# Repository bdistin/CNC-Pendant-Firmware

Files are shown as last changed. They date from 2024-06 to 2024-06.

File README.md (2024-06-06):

# CNC-Pendant-Firmware

This is firmware to run on an Arduino Pro Micro (preferred) or Arduino Nano to interface a popular style of wired CNC pendant to the PanelDue port of Duet electronics. Build it using Arduino IDE. 

For a full guide to building the pendant, see [the Duet3D wiki here](https://docs.duet3d.com/en/User_manual/Connecting_hardware/IO_CNC_Pendant).

## Fork Notes

This is a fork meant to adapt a D15 ended MPG. This has minor modifications due to the specific wiring of an off the shelf MPG. Please verify your specific MPG wiring
against the below diagram. 
```
     ________________________________________
    / GND  A-   B-   YIN  4    X10   EP      \
   / 5v   A+   B+   XIN  ZIN  X100  5    COM  \
   --------------------------------------------
     ______________________
    / 9  10 11 12 13 14 15 \
   / 1  2  3  4  5  6  7  8 \
   --------------------------
```
Because of the available pins this is slightly less capable than the Head of this fork. There is no way to control the LED, nor a way to differenciate between No Axis
and the 6th Axis. The X1 multiplier setting is possible with the adjusted logic in this fork by only checking the X10/X100 pins.

## Pendant to Arduino Pro Micro connections

| Function | D15 Pin | Pro Micro |
|:---|:---|:---|
| 5v | 1 | VCC |
| A+ | 2 | D10 |
| B+ | 3 | D14 |
| XIN | 4 | D2 |
| ZIN | 5 | D4 |
| X100 | 6 | D6 |
| Axis5 | 7 | D9 |
| GND/COM | 8, 9, 16 | GND |
| YIN | 12 | D3 |
| Axis4 | 13 | D5 |
| X10 | 14 | D7 |
| EStop | 15 | D8 |

Arduino Pro Micro to Duet 3 IO_0 connector or Duet 2 PanelDue connector wiring (3- or 4-core cable):

| Pro Micro | Duet |
|:---|:-----|
| VCC | +5V (red wire) |
| GND | GND (yellow wire) |
| TXO<br>GND | Through 6K8 resistor to IO_0_IN (Duet 3) or URXD0 (Duet 2)<br>Also connect 10K resistor between GND and IO_0_IN (Duet 3) or URXD0 (Duet 2) (blue wire from resistor junction to Duet) |

To connect a PanelDue as well (the Arduino Pro Micro passes the PanelDue commands through to the Duet):

| PanelDue | Pro Micro / Duet |
|:---|:---|
| +5V | +5V/VCC (red wire to Ardiuno or Duet) |
| GND | GND (yellow wire to Ardiuno or Duet) |
| DIN | **Duet** IO_0_OUT (Duet 3) or UTXD0 (Duet 2) (green wire) |
| DOUT | **Pro Micro** RXI (blue wire of PanelDue cable to green wire of pendant cable) |

For wiring differences and hardware changes needed if using an Arduino Nano, see the comments at the start of the CNC-pendant.ino file.

## Support requests

Please use the [forum](https://forum.duet3d.com) for support requests.

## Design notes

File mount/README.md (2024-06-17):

# Din Rail Mount
This is a printable model to adapt the PCB to a din rail mount using the Voron Din Clip found here: https://github.com/VoronDesign/Voron-Trident/blob/main/STLs/ElectronicsBay/pcb_din_clip_x3.stl

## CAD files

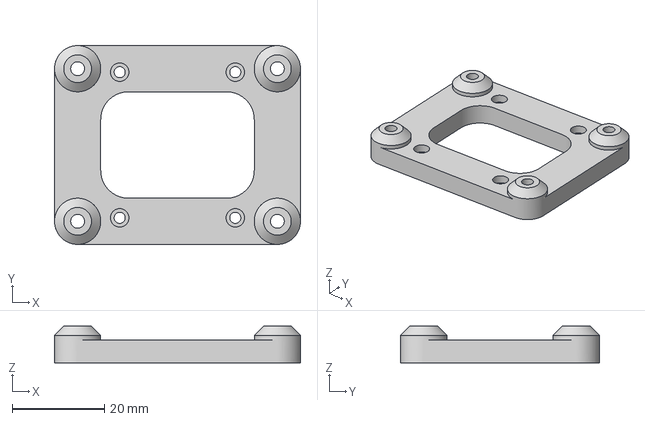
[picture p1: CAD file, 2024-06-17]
mount/Din Mount Adapter.3mf
53.2 x 43.0 x 8.00 mm

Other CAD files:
mount/Din Mount Adapter.f3d

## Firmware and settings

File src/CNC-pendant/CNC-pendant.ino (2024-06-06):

// CNC pendant interface to Duet
// D Crocker, started 2020-05-04

/* This Arduino sketch can be run on either Arduino Nano or Arduino Pro Micro. 
 * It should alo work on an Arduino Uno (using the same wiring scheme as for the Nano) or Arduino Leonardo (using the same wiring scheme as for the Pro Micro).
 * The recommended board is the Arduino Pro Micro because the passthrough works without any modificatoins to the Arduino. 

/* This is a fork meant to adapt a D15 ended MPG. This has minor modifications due to the specific wiring of an off the shelf MPG. Please verify your specific MPG wiring
 * against the below diagram. 
 *   ________________________________________
 *  / GND  A-   B-   YIN  4    X10   ES      \
 * / 5v   A+   B+   XIN  ZIN  X100  5    COM  \
 * --------------------------------------------
 *   ______________________
 *  / 9  10 11 12 13 14 15 \
 * / 1  2  3  4  5  6  7  8 \
 * --------------------------
 * Note: Because of the available pins this is slightly less capable than the Head of this fork. There is no way to control the LED, nor a way to differentiate between No Axis
 * and the 6th Axis. The X1 multiplier setting is possible with the adjusted logic in this fork by only checking the X10/X100 pins.

*** Pendant to Arduino Pro Micro connections ***

Function    D15 Pin    Pro Micro
5v          1          VCC
A+          2          D10
B+          3          D14
XIN         4          D2
ZIN         5          D4
X100        6          D6
Axis5       7          D9
GND/COM     8, 9, 16   GND
YIN         12         D3
Axis4       13         D5
X10         14         D7
EStop       15         D8

*** Arduino Pro Micro to Duet PanelDue connector connections ***

Pro Micro Duet
VCC       +5V
GND       GND
TX1/D0    Through 6K8 resistor to URXD, also connect 10K resistor between URXD and GND

To connect a PanelDue as well:

PanelDue +5V to +5V/VCC
PanelDue GND to GND
PanelDue DIN to Duet UTXD or IO_0_OUT
PanelDue DOUT to /Pro Micro RX1/D0.

*** Arduino Nano to Duet PanelDue connector connections ***

Nano    Duet
+5V     +5V
GND     GND
TX1/D0  Through 6K8 resistor to URXD, also connect 10K resistor between URXD and GND

To connect a PanelDue as well:

PanelDue +5V to +5V
PanelDue GND to GND
PanelDue DIN to Duet UTXD or IO_0_OUT
PanelDue DOUT to Nano/Pro Micro RX1/D0.

On the Arduino Nano is necessary to replace the 1K resistor between the USB interface chip by a 10K resistor so that PanelDiue can override the USB chip.
On Arduino Nano clones with CH340G chip, it is also necessary to remove the RxD LED or its series resistor.

*/

// Configuration constants
const int PinA = 10;
const int PinB = 14;
const int PinX = 2;
const int PinY = 3;
const int PinZ = 4;
const int PinAxis4 = 5;
const int PinAxis5 = 9;
const int PinStop = 8;
const int PinTimes10 = 7;
const int PinTimes100 = 6;

const unsigned long BaudRate = 57600;
const int PulsesPerClick = 4;
const unsigned long MinCommandInterval = 20;
const int HoldTime = 1000;

// Table of commands we send, one entry for each axis
const char* const MoveCommands[] = {
  "G91 G0 F6000 X",     // X axis
  "G91 G0 F6000 Y",     // Y axis
  "G91 G0 F600 Z"      // Z axis
};

const char* Home = "G28";
const char* Park = "G27";
const char* EStop = "M112";
const char* Recover = "M999";

#include "RotaryEncoder.h"
#include "GCodeSerial.h"
#include "PassThrough.h"

RotaryEncoder encoder(PinA, PinB, PulsesPerClick);
PassThrough passThrough;

int serialBufferSize;
uint32_t whenLastCommandSent = 0;

const int axisPins[] = { PinX, PinY, PinZ, PinAxis4, PinAxis5 };

// Auto count axis array
const int numAxis = sizeof(axisPins) / sizeof(int);

#if defined(__AVR_ATmega32U4__)     // Arduino Leonardo or Pro Micro
# define UartSerial   Serial1
#elif defined(__AVR_ATmega328P__)   // Arduino Uno or Nano
# define UartSerial   Serial
#endif

GCodeSerial output(UartSerial);

// Prototype
void sendCommand(char* command, int distance=0);

// Setup
void setup() {
  pinMode(PinA, INPUT_PULLUP);
  pinMode(PinB, INPUT_PULLUP);
  pinMode(PinX, INPUT_PULLUP);
  pinMode(PinY, INPUT_PULLUP);
  pinMode(PinZ, INPUT_PULLUP);
  pinMode(PinAxis4, INPUT_PULLUP);
  pinMode(PinAxis5, INPUT_PULLUP);
  pinMode(PinTimes10, INPUT_PULLUP);
  pinMode(PinTimes100, INPUT_PULLUP);
  pinMode(PinStop, INPUT_PULLUP);

  output.begin(BaudRate);

  serialBufferSize = output.availableForWrite();

#if defined(__AVR_ATmega32U4__)     // Arduino Leonardo or Pro Micro
  TX_RX_LED_INIT;
#endif
}

// Check for received data from PanelDue, store it in the pass through buffer, and send it if we have a complete command
void checkPassThrough() {
  unsigned int commandLength = passThrough.Check(UartSerial);
  if (commandLength != 0 && UartSerial.availableForWrite() == serialBufferSize) output.write(passThrough.GetCommand(), commandLength);
}

void sendCommand(char* command, int distance) {
#if defined(__AVR_ATmega32U4__)     // Arduino Micro, Pro Micro or Leonardo
  TXLED0;                           // turn on transmit LED
#endif

  whenLastCommandSent = millis();
  output.write(command);
  if (distance != 0) output.print(distance/10.); // Need to send the binary of the ascii representation of the float rather than the binary of the float itself
  output.write('\n');
}

int pollDistanceMultiplier() {
  if (digitalRead(PinTimes10) == LOW) return 10;
  else if (digitalRead(PinTimes100) == LOW) return 100;
  return 1;
}

int pollAxis() {
  for (int i=0; i<numAxis; i++) if (digitalRead(axisPins[i]) == LOW) return i;
  return -1;
}

void eStop() {
    do {
      sendCommand(EStop);
      uint16_t now = (uint16_t)millis();

      while (digitalRead(PinStop) == HIGH && (uint16_t)millis() - now < 2000) checkPassThrough();

      encoder.getChange();      // ignore any movement
    } while (digitalRead(PinStop) == HIGH);

    sendCommand(Recover);
}

void loop() {
#if defined(__AVR_ATmega32U4__)     // Arduino Micro, Pro Micro or Leonardo
    TXLED1;                         // turn off transmit LED
#endif

  // 0. Poll the encoder. Ideally we would do this in the tick ISR, but after all these years the Arduino core STILL doesn't let us hook it.
  // We could possibly use interrupts instead, but if the encoder suffers from contact bounce then that isn't a good idea.
  // In practice this loop executes fast enough that polling it here works well enough
  encoder.poll();

  if (output.availableForWrite() == serialBufferSize) { // No sense checking inputs and doing calculations if we can't send a command

    // 1. Check for emergency stop
    if (digitalRead(PinStop) == HIGH) eStop();

    // 2. Poll the feed amount switch
    int distanceMultiplier = pollDistanceMultiplier();

    // 3. Poll the axis selector switch
    int axis = pollAxis();
    
    // 4. Send a command based on the accumulated data if criteria is met.
    if ((uint32_t)millis() - whenLastCommandSent >= MinCommandInterval) {
      int distance = encoder.getChange() * distanceMultiplier;
      if (axis == 4) { // No Axis 5, so see if we should home. Distance is discarded.
        delay(HoldTime);
        if (digitalRead(PinAxis5) == LOW) {
          sendCommand(Home);
          delay(HoldTime); // Prevent Double Calls
        }
      } else if (axis == 3) { // No Axis 4, so see if we should park. Distance is discarded.
        delay(HoldTime);
        if (digitalRead(PinAxis4) == LOW) {
          sendCommand(Park);
          delay(HoldTime); // Prevent Double Calls
        }
      } else if (axis >= 0 && distance != 0) { // Move X, Y, or Z
        sendCommand(MoveCommands[axis], distance);
      }
    }
  }

  // 5. Check if there is passthrough data from the PanelDue
  checkPassThrough();
}

// End

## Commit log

2024-06-06 Share PCB efforts
    [ddcs-expert-to-rrf.fzz]
2024-06-17 Add Din Mount Adapter 3d print
    [Din Mount Adapter.3mf, Din Mount Adapter.f3d]
